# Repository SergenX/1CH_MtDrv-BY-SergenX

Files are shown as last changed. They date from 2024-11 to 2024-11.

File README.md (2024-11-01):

# 1CH_MtDrv-BY SergenX
 60A 7S Smart Motor Driver

Hello GitHub User :)))

I designed a single channel brake motor driver and I share it as open source and I will also make a 2nd version of it. 
So what features does this pcb board have?

1CH_MtDrv Features Version 1;

Voltage , Current , Temperature and Encoder reading.

Automatic current voltage and temperature limiter.

Close Loop Encoder Calucator.

Position Control (not added just tested working!)

Magnetic shaft lock output (MAX 10A)

CANBUS Interface - (not added)

RS485 Interface - Added

32 Bit Arm Cortex M0 CPU 32KB Flash 6KB RAM

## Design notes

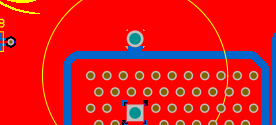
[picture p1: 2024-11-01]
1CH_MtDrv_R01_V1-0924/Design Mistakes/GND Poly 2.png

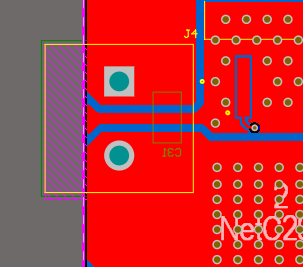
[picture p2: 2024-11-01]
1CH_MtDrv_R01_V1-0924/Design Mistakes/GND Poly.png

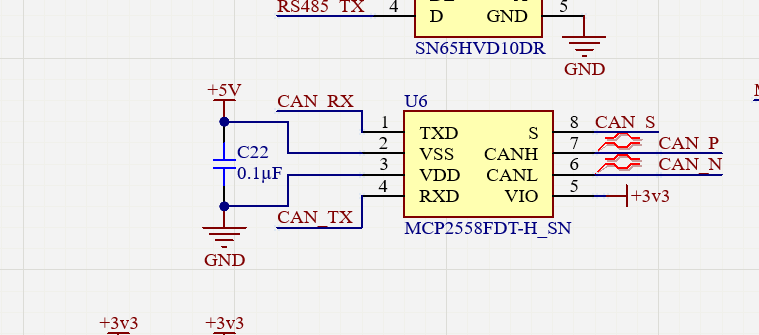
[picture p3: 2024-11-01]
1CH_MtDrv_R01_V1-0924/Design Mistakes/Reverse CAN Power Pins.png

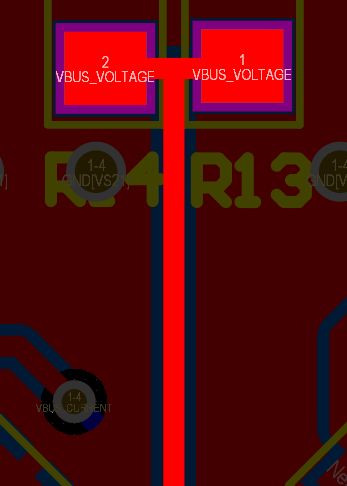
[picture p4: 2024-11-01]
1CH_MtDrv_R01_V1-0924/Design Mistakes/Teardrops.png

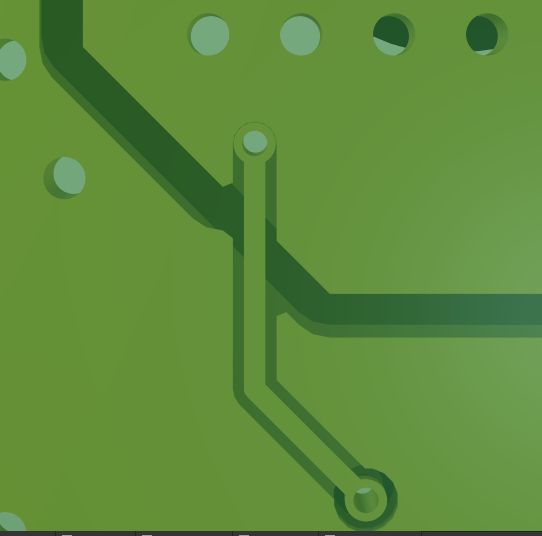
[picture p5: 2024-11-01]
1CH_MtDrv_R01_V1-0924/Design Mistakes/VBUS Via.png

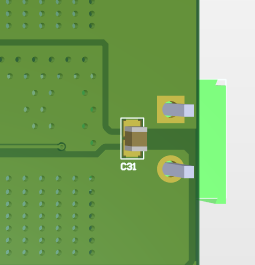
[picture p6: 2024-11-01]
1CH_MtDrv_R01_V1-0924/Design Mistakes/not important.png

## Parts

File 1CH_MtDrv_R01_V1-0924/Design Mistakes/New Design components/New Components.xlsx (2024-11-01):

Component Name | Desc. | Changing designator
XT60 Male | Robust than Green Terminal - Peak 30 Rated 60A Connector | J3
SWD Program | 4 pin smd program pin (not adding component) | J1
10uF 0805 | 10uF 1206 Changed | C9,C3
7461383 | Wurth Redcube Series 180A | J4 (Motor Outputs)
470uF 63V | Electrolytic Capacitor | C25

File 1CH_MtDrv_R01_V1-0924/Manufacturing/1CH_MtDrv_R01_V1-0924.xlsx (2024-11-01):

Line # | Name | Description | Designator | Quantity | Manufacturer 1 | Manufacturer Part Number 1 | Manufacturer Lifecycle 1 | Supplier 1 | Supplier Part Number 1 | Supplier Unit Price 1 | Supplier Subtotal 1
* | 4.7 µF 50V | 10 uF 50V 1206 | C1, C7 | 2
* | 0.1µF | 0.1uF 0805 Surface Capacitor | C2, C8 | 2
* | 10µF 50V | 10 uF 50V 1206 | C3, C9 | 2
* | 1µF | 1uF 0603 Surface Capacitor | C4, C5, C18, C27, C28 | 5
* | 10nF | 10nF 0603 Surface Capacitor | C6, C17 | 2
* | 0.1µF | 0.1uF 0603 Surface Capacitor | C10, C11, C12, C13, C16, C19, C22, C23, C24, C26 | 10
* | 4.7µF | 4.7uF 0603 Surface Capacitor | C14, C15 | 2
 | 18pF | 18pF 0603 Surface Capacitor | C20, C21 | 2
* | 1000 µF 50V | 1000µF 50V Aluminum Electrolytic Capacitors Radial, Can 2000 Hrs @ 85Â°C | C25 | 1
* | 2.2µF | 2.2uF 0805 Surface Capacitor | C29, C30 | 2
* | 0.22µF | 0.22uF 0805 Surface Capacitor | C31 | 1
* | LTST-C190TGKT | 20mA Generic 0603 Led SMD | D1, D4, D5 | 3
* | SS26-E3_52T | 2A SMD Schottky Diode | D2, D3 | 2
* | LCB2012-152Y-N | Ferrite Bead 1A 0805 SMD | FB1 | 1
* | 5 Pin 2.54mm Header | Generic 2.54MM 5 Pin Header | J1 | 1
* | DS1034-09FBNSISS | CONNECTOR DSUB 9PIN 180C PCB TYPE FEMALE | J2 | 1
* | 282856-2 | TERMI-BLOK PCB MOUNT 2P | J3, J4, J5 | 3
* | IHLP2525CZER220M8A | Fixed Inductor 22uH 2.8A 174 mOHM SMD | L1, L2 | 2
 | SQM110N05-06L_GE3 | MOSFET DIS.110A 55V N-CH | Q1, Q2, Q3, Q4 | 4
* | SUD50P04-08-GE3 | MOSFET (P-Channel) 50V 40A 8mOhms | Q5 | 1
* | BC817-40,215 | 0.5A 45V BJT NPN Transistor SOT23 SMD | Q6 | 1
* | 49.9 kOhms | 49.9 kOhms 0603 | R1 | 1
* | 330 Ohms | 330 Ohm 0603 | R2, R6, R7, R28 | 4
* | 9.53 kOhms | 9.53 kOhms 0603 | R3 | 1
* | 47 kOhms | 47 kOhm 0603 | R4 | 1
* | 3.3 kOhms | 3.3 kOhms 0603 | R5 | 1
* | 4.7 kOhms | 4.7 kOhms 0603 | R8 | 1
* | 0 Ohms | 0 Ohm 0603 | R9, R10, R11 | 3
* | 1 kOhms | 1 kOhms 0603 | R12 | 1
* | 100 kOhms | 100k Ohm 0603 | R13, R17, R18 | 3
* | 12.1 kOhms | 12.1 kOhms 0603 | R14 | 1
* | 51 kOhms | 51k Ohm 0603 | R15, R16 | 2
* | 10 kOhms | 10 kOhms 0603 | R19, R20, R29, R30 | 4
* | BVT-I-R003-1.0 | 3mOhm Resistor 2510 SMD Package | R21 | 1
* | 54.9 kOhms | 54.9k Ohm 0603 | R22 | 1
* | 47 Ohms | 47 Ohm 0603 | R23, R24, R25, R26 | 4
* | 100 Ohms | 100 Ohm 0603 | R27 | 1
* | AOZ1282CI | +36V 1.2A Buck Converter | U1, U3 | 2
* | LD3985M33R | IC REG LIN 3.3V 150MA TSOT23-5 | U2 | 1
* | STM32F042C6U6 | STMICROELECTRONICS - STM32F042C6U6 - MCU, ARM CORTEX-M0, 48MHZ, UFQFPN-48 | U4 | 1
* | SN65HVD10DR | 3.3V RS485 TRANSRECEIVER IC | U5 | 1
* | MCP2562T-E/SN | CAN Interface IC CAN Transceiver with Silent Mode | U6 | 1
* | M24C01-WMN6TP | EEPROM Memory IC 1Kb (128 x 8) IÂ²C 400kHz 900ns 8-SO | U7 | 1
* | INA139NA_3K | %0.5 Current Monitor 60V Analog SMD | U8 | 1
* | UCC27201ADR | 3-A, 120-V half bridge gate driver with 8-V UVLO and negative voltage handling | U9, U10 | 2
* | ABM3-8.000MHZ-D2Y-T | 8MHz 2 Pin SMD Crystal | XTAL1 | 1

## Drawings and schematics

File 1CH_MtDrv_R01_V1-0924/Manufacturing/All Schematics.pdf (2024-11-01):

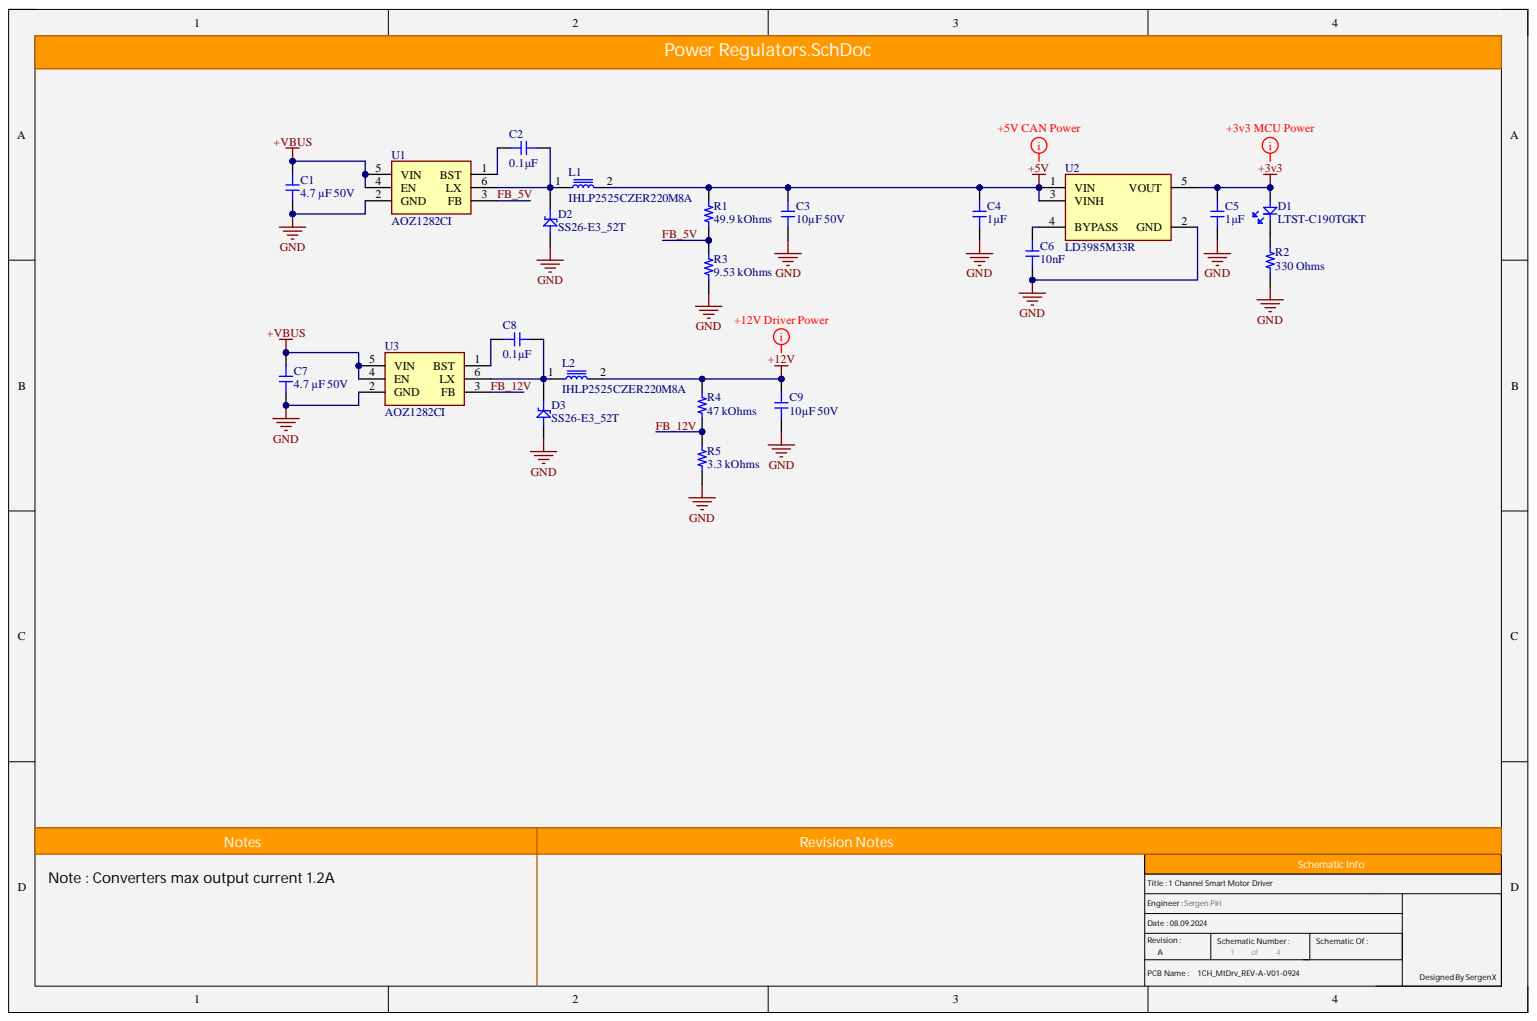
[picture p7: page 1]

Not e s | Revision Notes

I nfo

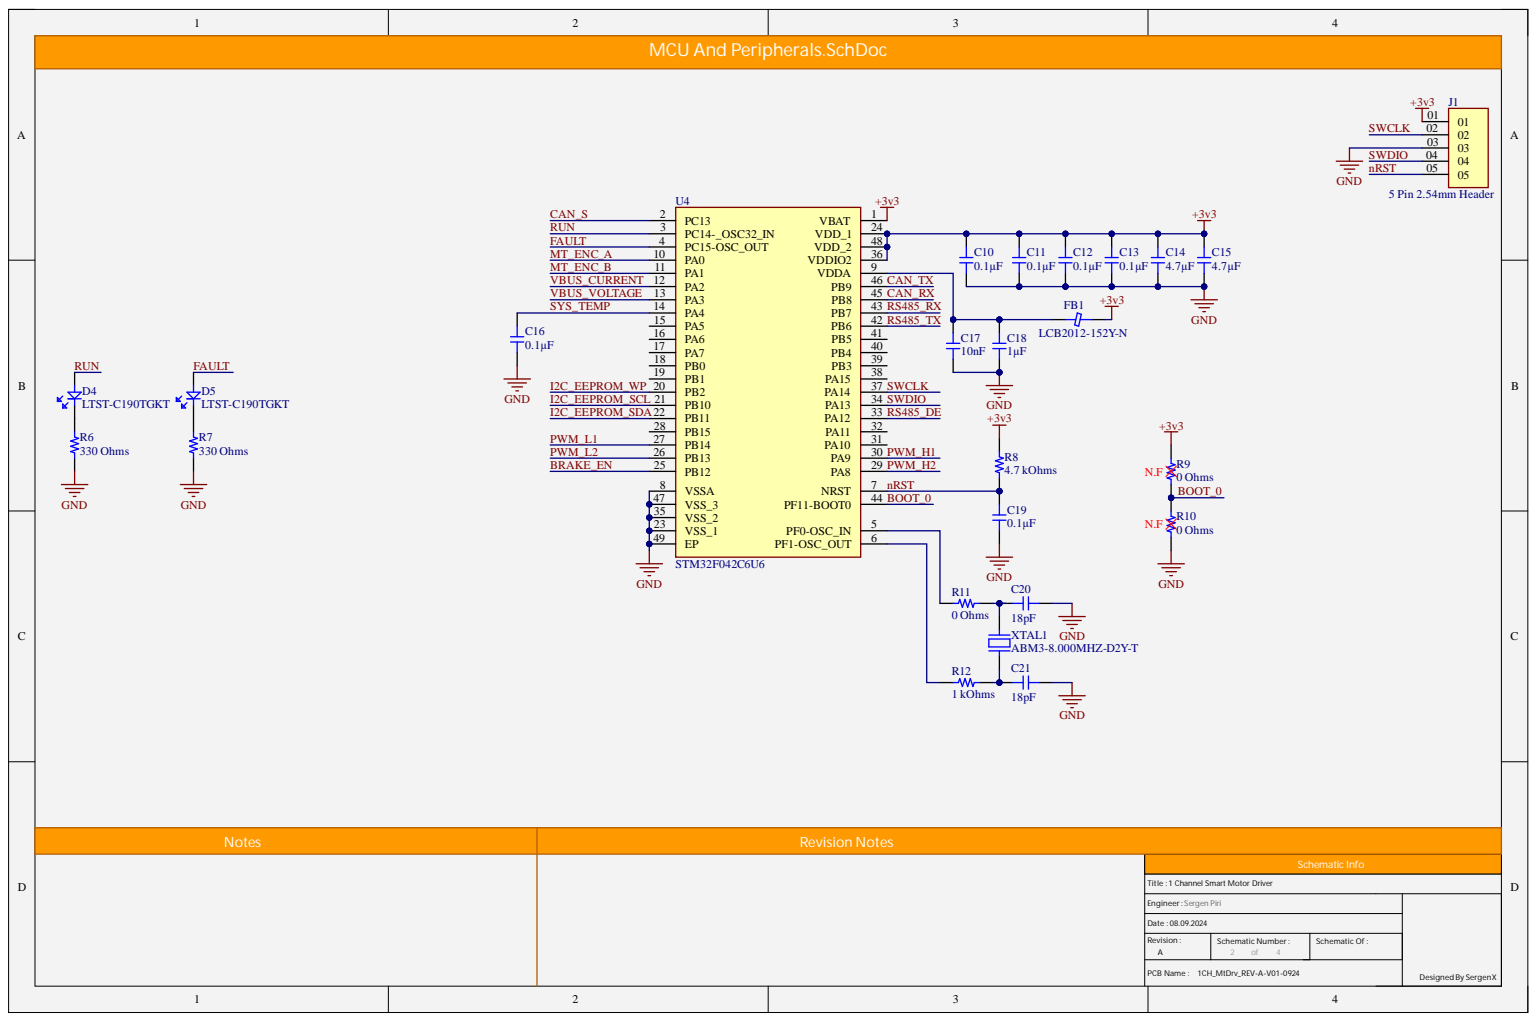
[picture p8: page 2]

Not e s | Revision Notes

I nfo

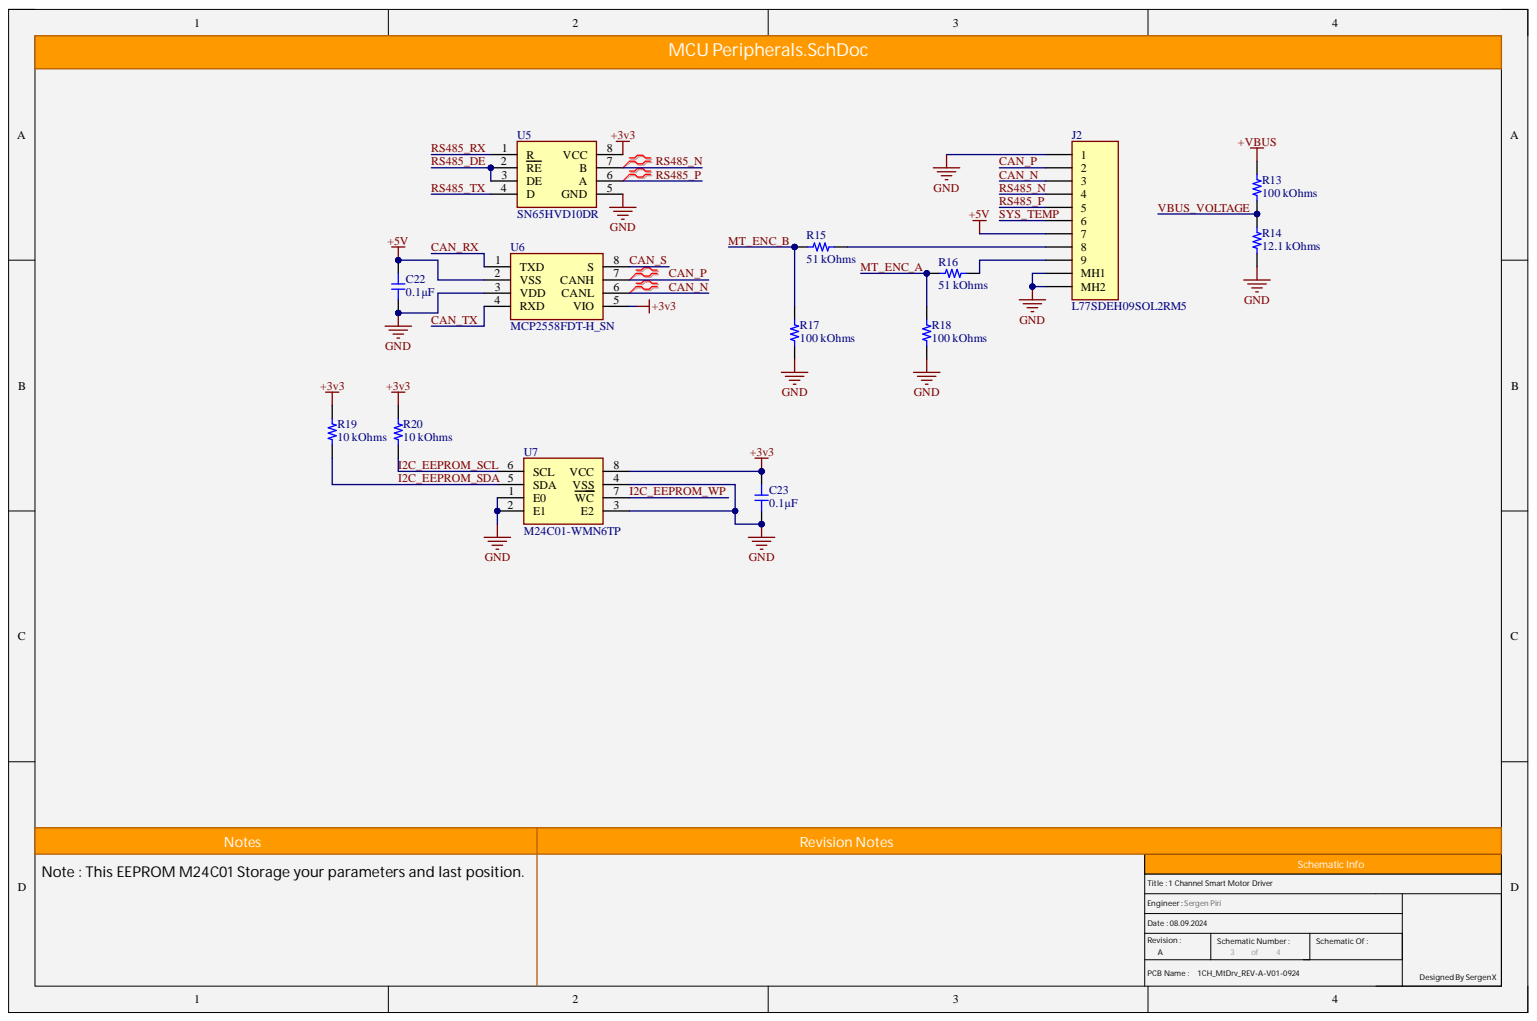
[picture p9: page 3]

Not e s | Revision Notes

I nfo

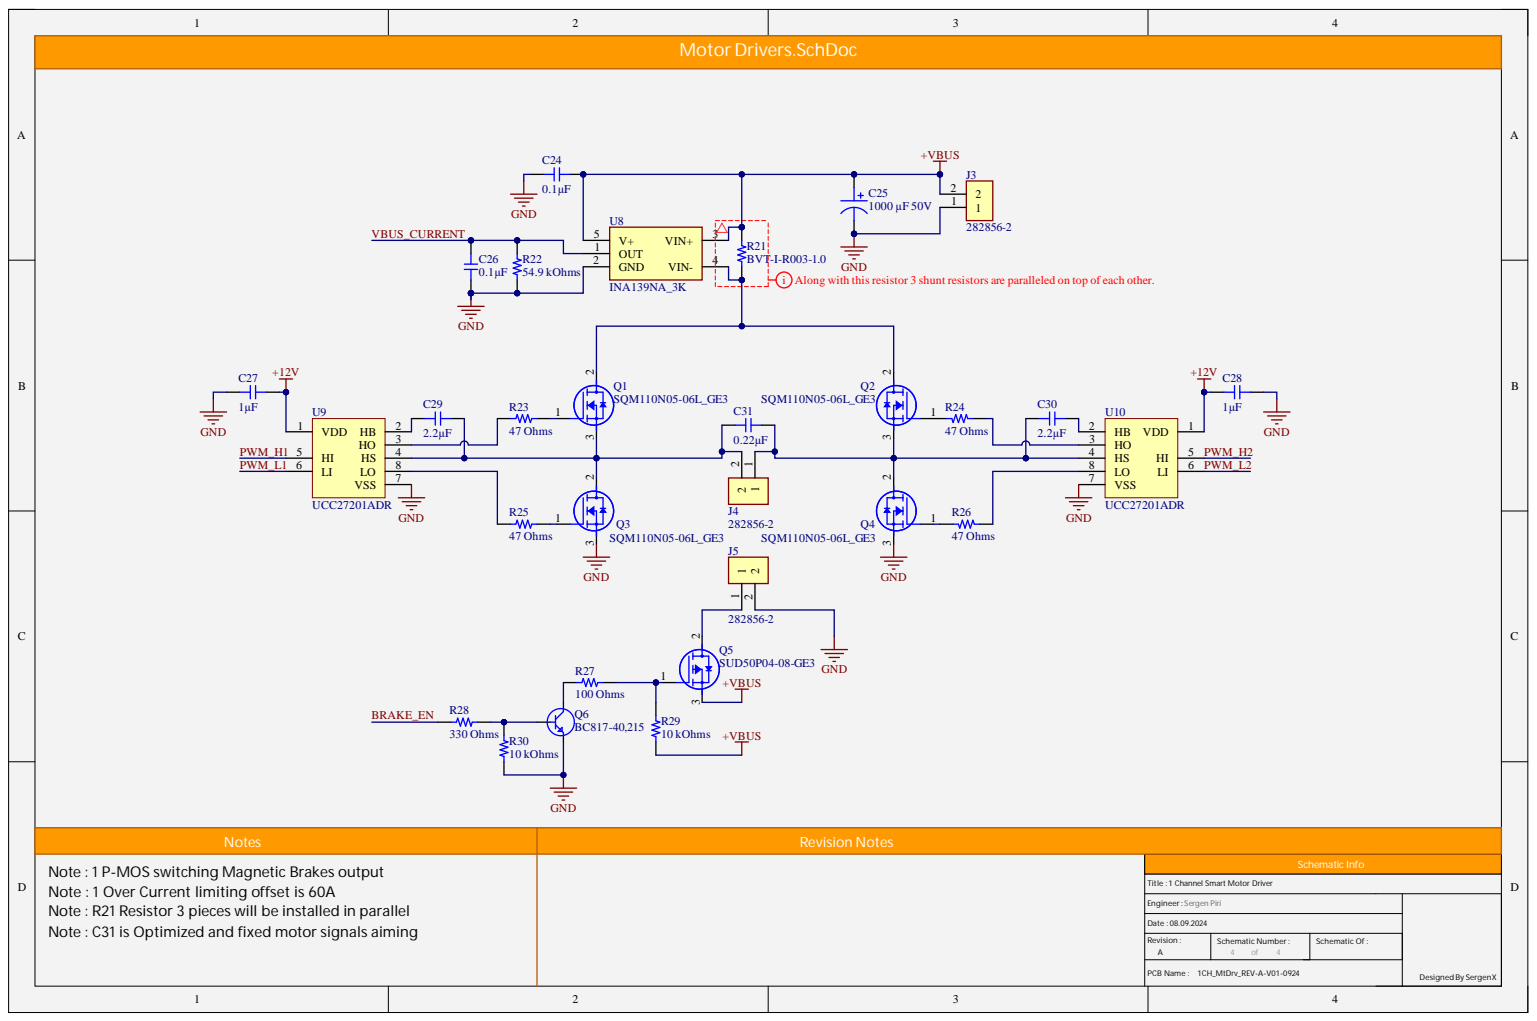
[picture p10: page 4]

OUT 1 VIN- | 4

0.1µF 54.9 kOhms

i Along with this resistor 3 shunt resistors are paralleled on top of each other.

Notes | Revision Notes

Note : 1 P-MOS switching Magnetic Brakes output
Note : 1 Over Current limiting offset is 60A
Note : R21 Resistor 3 pieces will be installed in parallel
Note : C31 is Optimized and fixed motor signals aiming

Schematic Info

1 Channel Smart Motor Driver

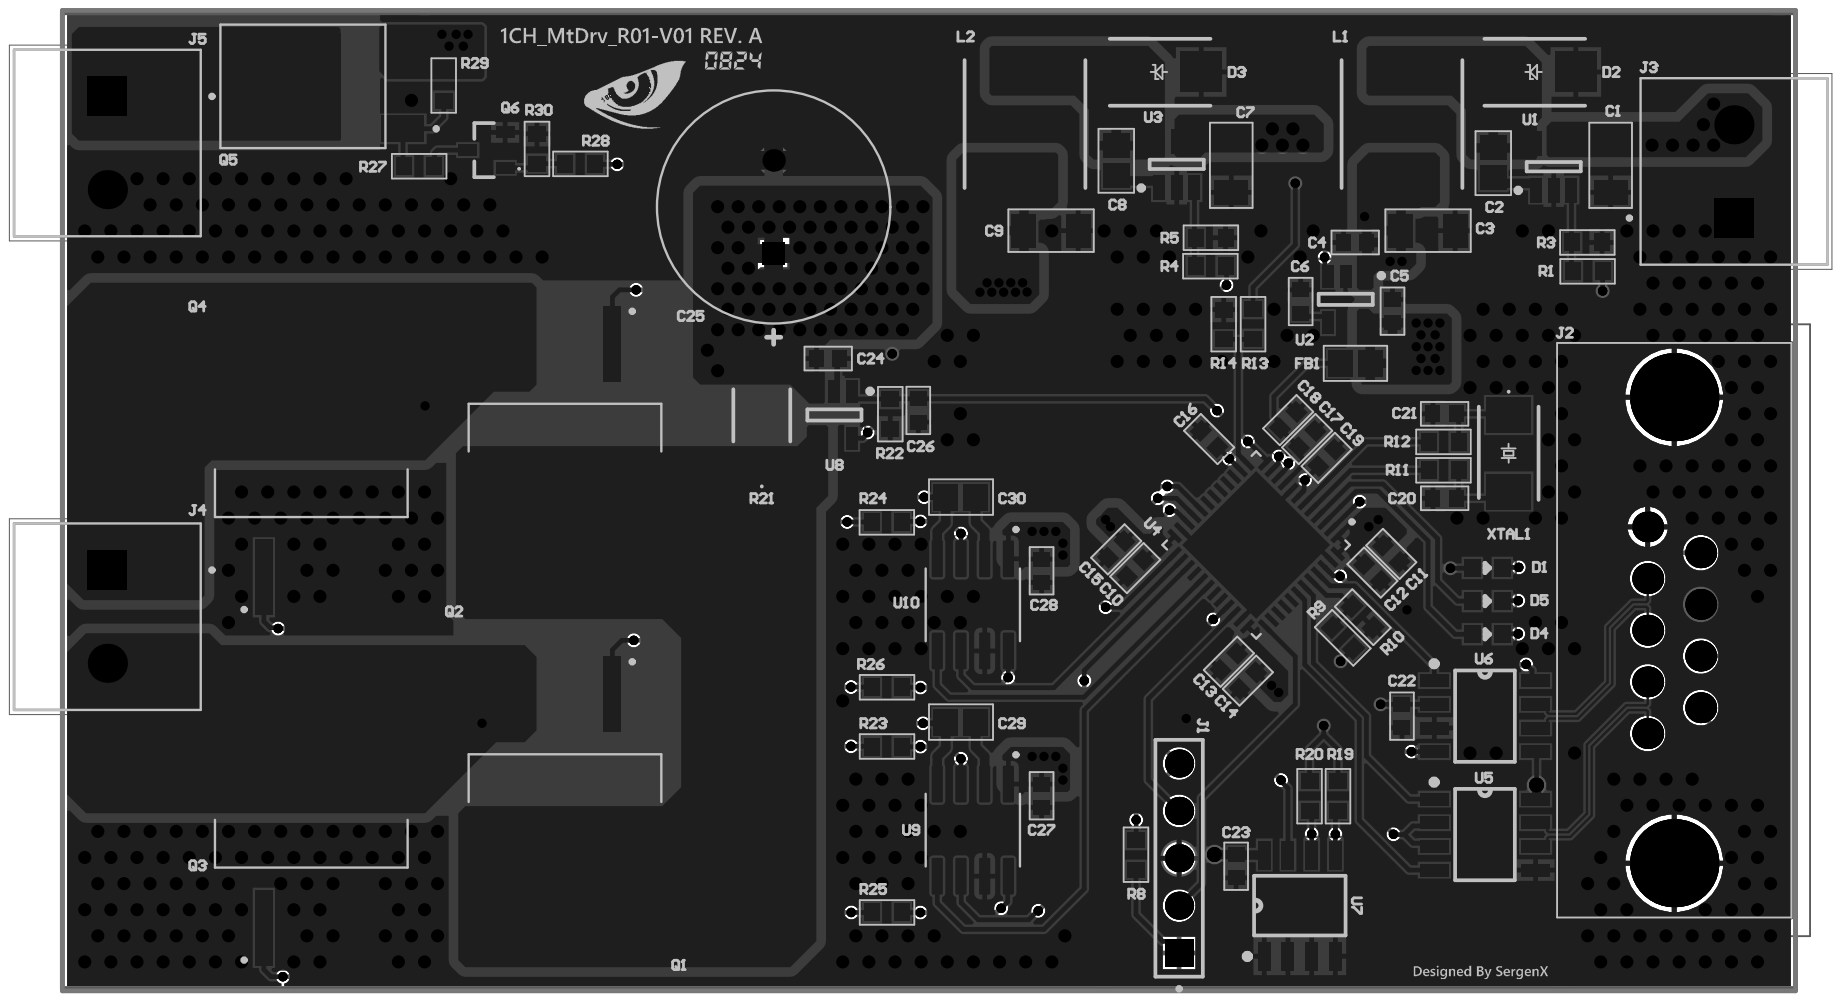
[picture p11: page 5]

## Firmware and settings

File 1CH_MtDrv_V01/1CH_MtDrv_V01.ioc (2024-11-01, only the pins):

Mcu.UserName=STM32F042C6Ux
PA0.GPIO_Label=ENC_B
PA0.Signal=S_TIM2_CH1_ETR
PA1.GPIO_Label=ENC_A
PA1.Signal=S_TIM2_CH2
PA13.Signal=SYS_SWDIO
PA14.Signal=SYS_SWCLK
PA2.GPIO_Label=CURRENT
PA2.Signal=ADC_IN2
PA3.GPIO_Label=VOLTAGE
PA3.Signal=ADC_IN3
PA4.GPIO_Label=TEMP
PA4.Signal=ADC_IN4
PA8.Signal=S_TIM1_CH1
PA9.Signal=S_TIM1_CH2
PB10.Signal=I2C1_SCL
PB11.Signal=I2C1_SDA
PB12.GPIO_Label=BRAKE
PB12.Signal=GPIO_Output
PB13.Signal=TIM1_CH1N
PB14.Signal=TIM1_CH2N
PB6.Signal=USART1_TX
PB7.Signal=USART1_RX
PC14OSC32_IN.GPIO_Label=RUN
PC14OSC32_IN.Signal=GPIO_Output
PC15OSC32_OUT.GPIO_Label=FAULT
PC15OSC32_OUT.Signal=GPIO_Output
PF0-OSC_IN.Signal=RCC_OSC_IN
PF1-OSC_OUT.Signal=RCC_OSC_OUT

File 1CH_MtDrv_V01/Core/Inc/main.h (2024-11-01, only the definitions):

#define RUN_Pin GPIO_PIN_14
#define RUN_GPIO_Port GPIOC
#define FAULT_Pin GPIO_PIN_15
#define FAULT_GPIO_Port GPIOC
#define ENC_B_Pin GPIO_PIN_0
#define ENC_B_GPIO_Port GPIOA
#define ENC_A_Pin GPIO_PIN_1
#define ENC_A_GPIO_Port GPIOA
#define CURRENT_Pin GPIO_PIN_2
#define CURRENT_GPIO_Port GPIOA
#define VOLTAGE_Pin GPIO_PIN_3
#define VOLTAGE_GPIO_Port GPIOA
#define TEMP_Pin GPIO_PIN_4
#define TEMP_GPIO_Port GPIOA
#define BRAKE_Pin GPIO_PIN_12
#define BRAKE_GPIO_Port GPIOB

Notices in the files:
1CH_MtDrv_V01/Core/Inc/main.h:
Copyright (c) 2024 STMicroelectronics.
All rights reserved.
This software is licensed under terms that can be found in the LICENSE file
